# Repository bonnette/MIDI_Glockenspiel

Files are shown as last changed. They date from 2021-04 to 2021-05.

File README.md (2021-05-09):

# Arduino MIDI controlled Glockenspiel
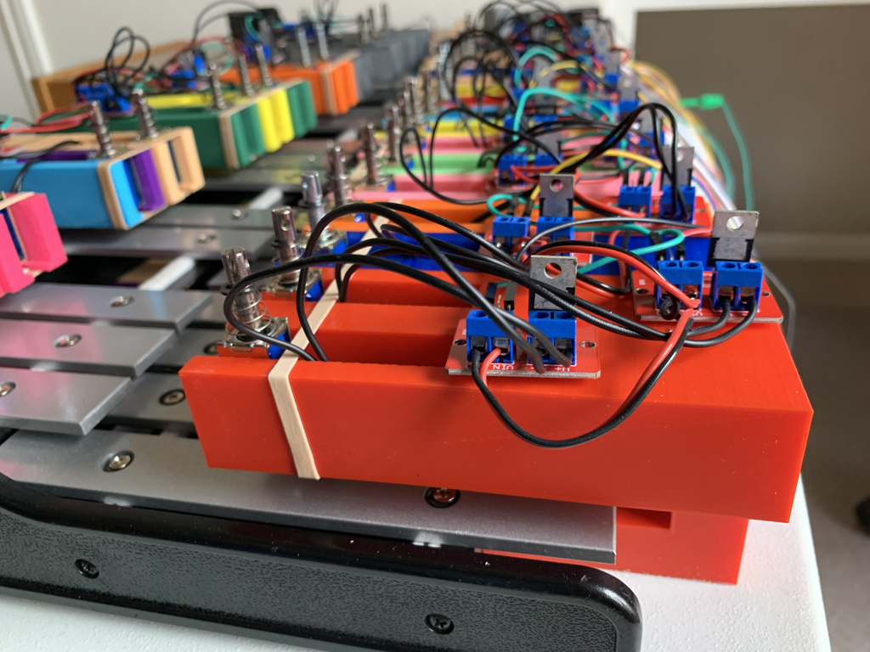
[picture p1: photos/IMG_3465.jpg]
Client Photo

<br/>
An automated Glockenspiel Arduino Project
Inspired by an Instructable
</br>
https://www.instructables.com/id/Making-the-Spielatron-Robotic-Glockenspiel/
</br>
See my AutoGlockenspiel repository for more information on my implementation of the "Instructable" project.</br>

The repository that you are currently looking at (although it was inspired by the Spielatron Instructable) is a totally different interpretation.
</br></br>
This project uses a Windows PC to drive an Arduino which fires one of 32 solenoids that sit above each note.
</br></br>
The MIDI control of the solenoids is accompished by using an Arduino Pro Mini. The serial connection between the Windows PC and the Arduino is through an FTDI interface. This interface allows music that has been converted to MIDI to be played on the Glockenspiel.
</br></br>
The Glockenspiel is a Pearl 32 note that I purchased from Ebay for $45
</br></br>
There is only one Arduino software program. This program uses the Arduino midi library to decode each MIDI note received from the PC. Then using I2C it sets one of 32 pins distributed across two MCP23017 I/O expander boards to a "HIGH" which then fires a solenoid that then strikes a note on the glockenspiel.</br>
The current program allows only one note at a time to be played. The use of LMMS on the PC provides you with the opportunity to direct MIDI to the Arduino on one track while the other tracks play on the computer. This makes for a very pleasant experience in that, you can listen to the glockenspiel along with the accompanying instruments playing on the PC. 
</br></br>
I designed holders for the solenoids. These holders fit on the bottom rails of the glockenspiel and align the solenoids over the keys. There are five different holders. Each holder takes approximately 4 hours to print. The difference in the holders is their location on the glockenspiel. There are three corner holders that hold two solenoids each. There are "High" holders which are all the same and there are "Low" holders. These are all the same as well. </br></br>
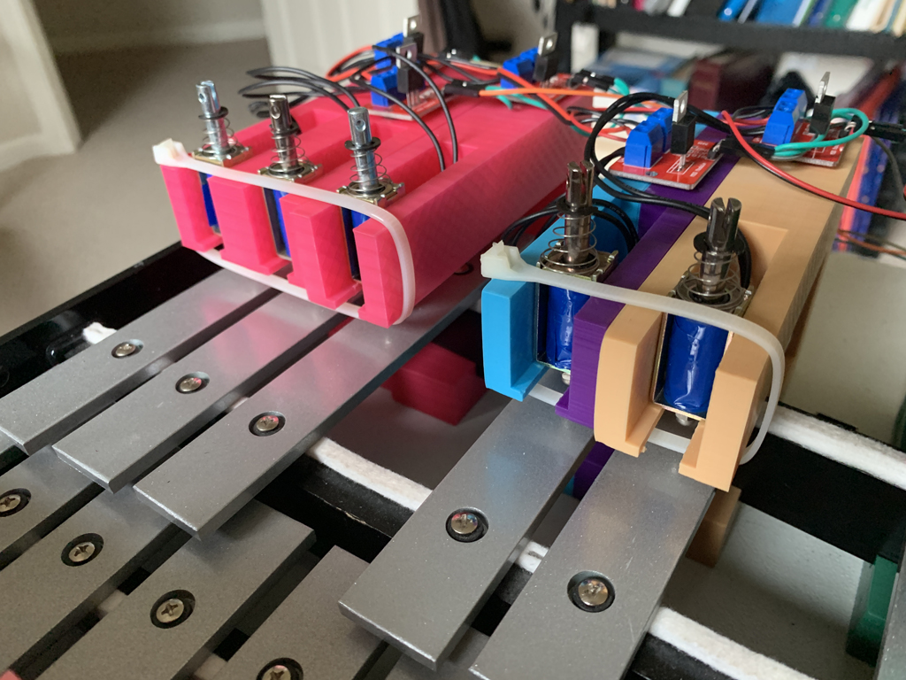
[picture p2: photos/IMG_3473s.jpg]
Client Photo

<br/>
The solenoids are held in place using zip ties.(Shown above). The zip ties are tied tight enough to hold the solinoids snuggly. 
</br></br>
A video of the glockenspiel playing a tune can be found here:</br>
https://youtu.be/QgNRVtduxMg
</br></br>
I used Fusion360 for the design of the solenoid holders and I thank Autodesk for allowing makers such as myself to use Fusion360 free of charge. Thanks Autodesk !</br>
I would also like to thank the developers of LMMS (https://lmms.io/) for their work.</br>
Thanks to hairless-midi (https://projectgus.github.io/hairless-midiserial/) for developing the Hairless MIDI Serial Bridge.</br>
and I also thank Tobias Erichsen for developing loopMIDI (https://www.tobias-erichsen.de/software/loopmidi.html). His software creates virtual loopback MIDI-ports which can then be used to connect the PC through a serial port (using the hairless-midi bridge) to the midi enabled glockenspiel.

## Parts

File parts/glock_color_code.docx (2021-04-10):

Note | Midi | Color | MCP Pin
F3 | 53 | Black | MCP A0 0
F3# | 54 | Brown | MCP A1 1
G3 | 55 | Red | MCP A2 2
G3# | 56 | Orange | MCP A3 3
A3 | 57 | Yellow | MCP A4 4
A3# | 58 | Green | MCP A5 5
B3 | 59 | Blue | MCP A6 6
C4 | 60 | Violet | MCP A7 7
C4# | 61 | Grey | MCP B0 8
D4 | 62 | White | MCP B1 9
D4# | 63 | Black | MCP B2 10
E4 | 64 | Brown | MCP B3 11
F4 | 65 | Red | MCP B4 12
F4# | 66 | Orange | MCP B5 13
G4 | 67 | Yellow | MCP B6 14
G4# | 68 | Green | MCP B7 15
A4 | 69 | Blue | MCP1 A0 0
A4# | 70 | Violet | MCP1 A1 1
B4 | 71 | Grey | MCP1 A2 2
C5 | 72 | White | MCP1 A3 3
C5# | 73 | Black | MCP1 A4 4
D5 | 74 | Brown | MCP1 A5 5
D5# | 75 | Red | MCP1 A6 6
E5 | 76 | Orange | MCP1 A7 7
F5 | 77 | Yellow | MCP1 B0 8
F5# | 78 | Green | MCP1 B1 9
G5 | 79 | Blue | MCP1 B2 10
G5# | 80 | Violet | MCP1 B3 11
A5 | 81 | Grey | MCP1 B4 12
A5# | 82 | White | MCP1 B5 13
B5 | 83 | Black | MCP1 B6 14
C6 | 84 | Brown | MCP1 B7 15

# MCP color code and pin assignment

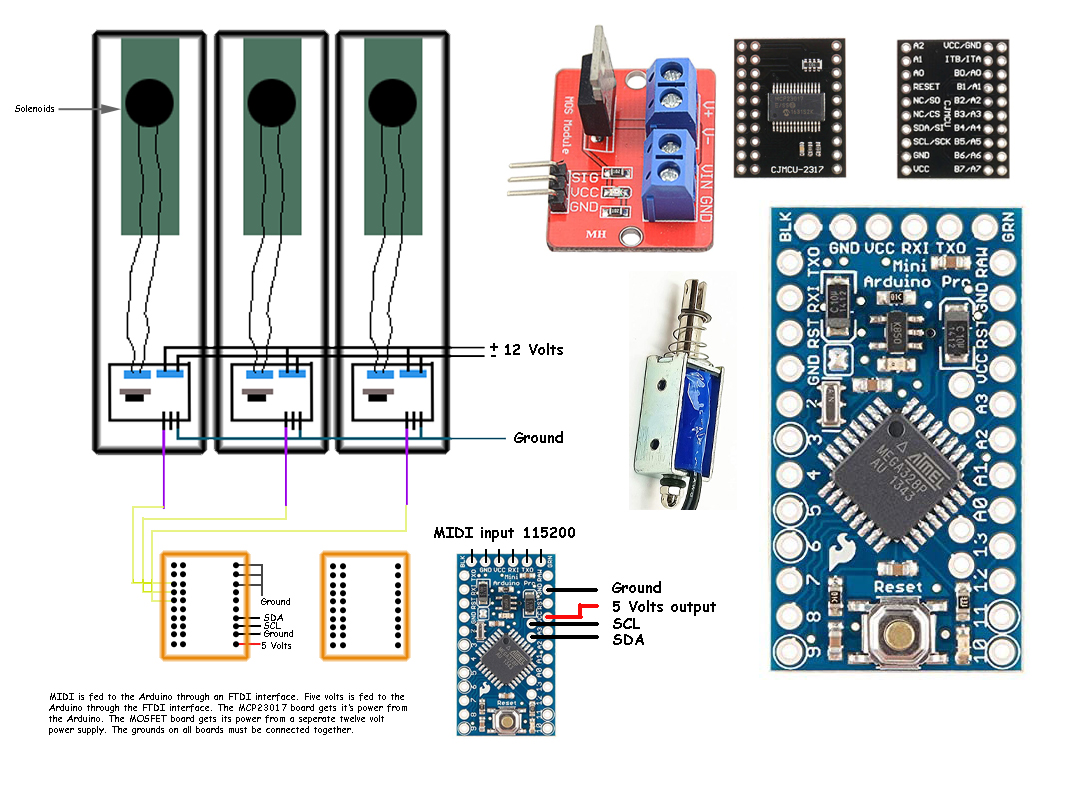
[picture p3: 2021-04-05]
parts/robo_glock.jpg

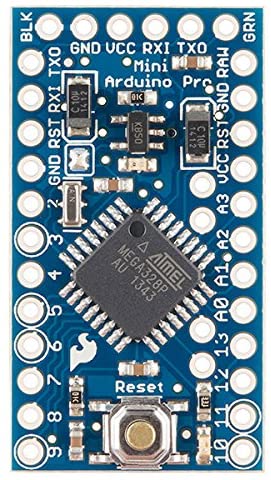
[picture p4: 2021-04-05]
parts/pro_mini.jpg

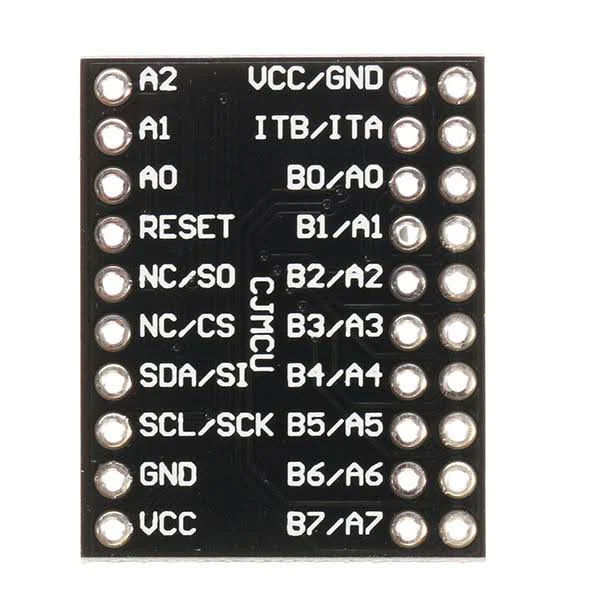
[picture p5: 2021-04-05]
parts/2317_back.jpg

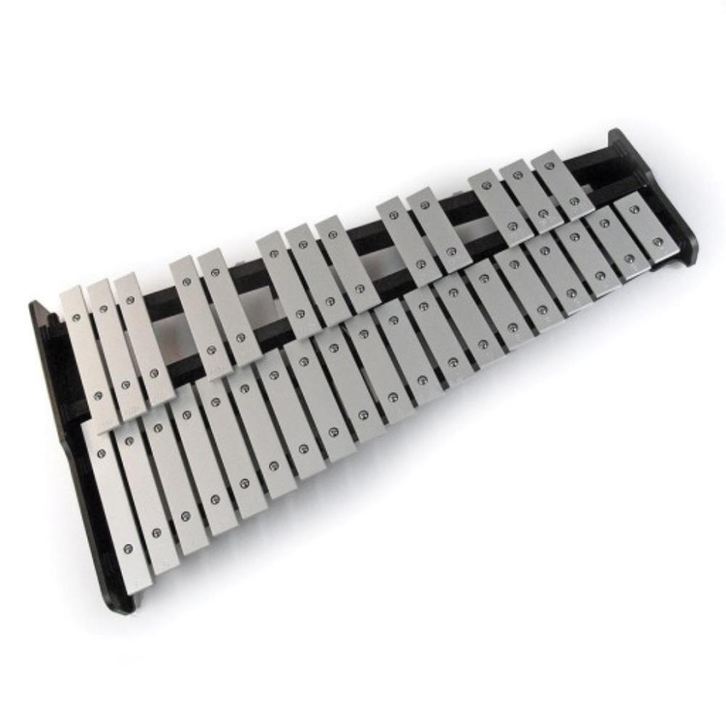
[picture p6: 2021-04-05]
parts/pearl_32.jpg

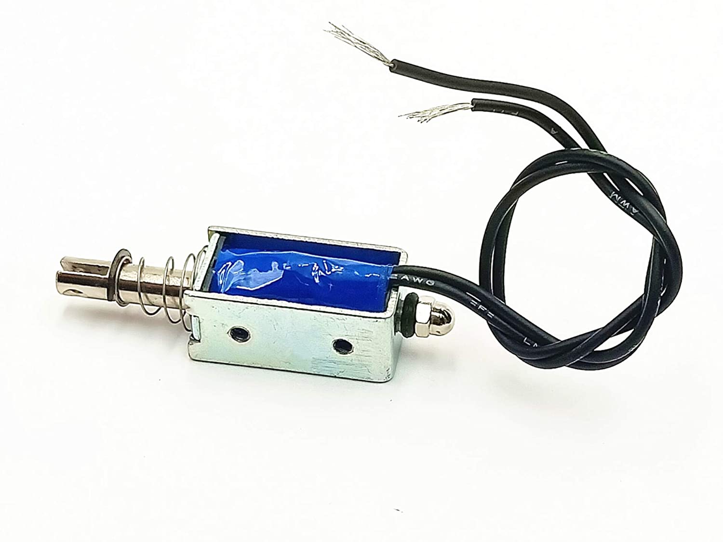
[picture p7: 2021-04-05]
parts/LYM_0530.jpg

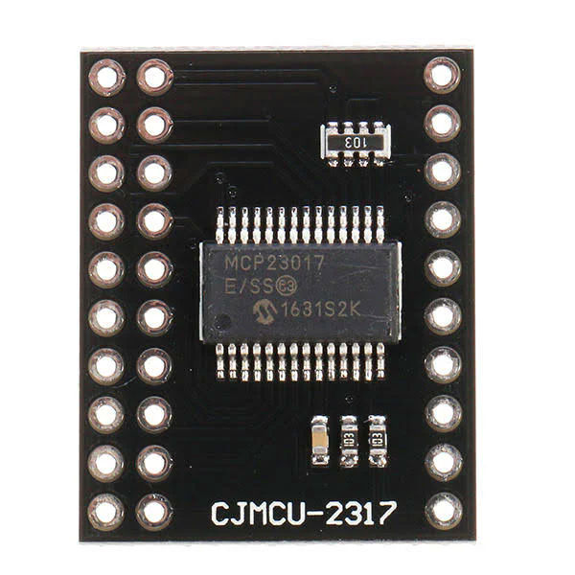
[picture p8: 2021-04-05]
parts/2317_front.jpg

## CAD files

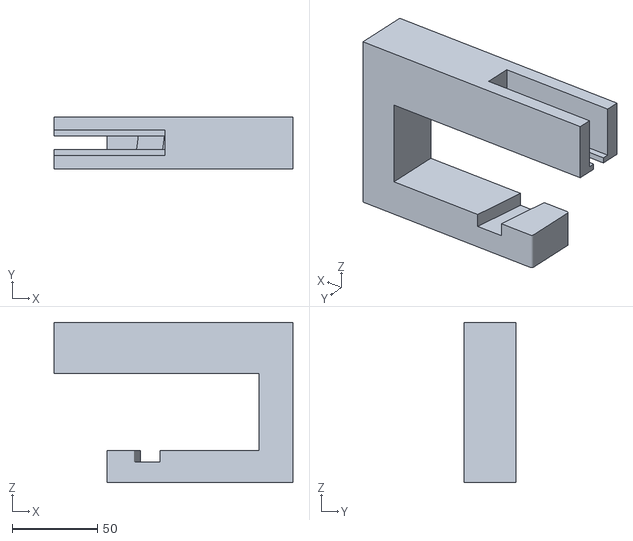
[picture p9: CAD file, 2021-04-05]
3D_printed/high_solenoid_hldr.stl
140.0 x 30.3 x 94.0

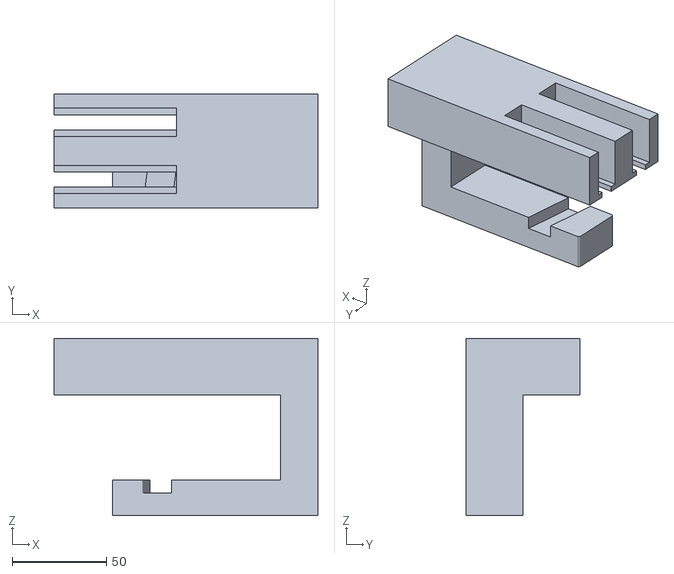
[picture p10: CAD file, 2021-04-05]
3D_printed/sol_hldr_hi_lft.stl
140.0 x 60.6 x 94.0

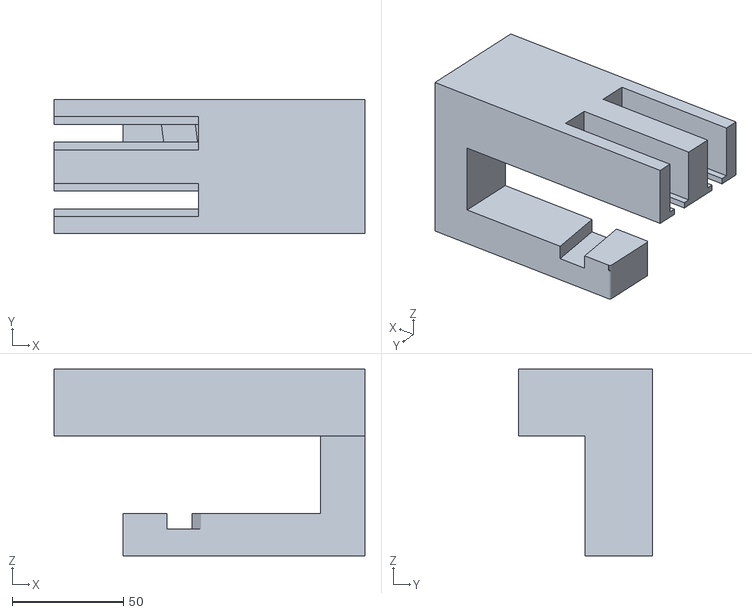
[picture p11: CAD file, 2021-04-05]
3D_printed/sol_hldr_lo_lft.stl
140.0 x 60.3 x 84.0

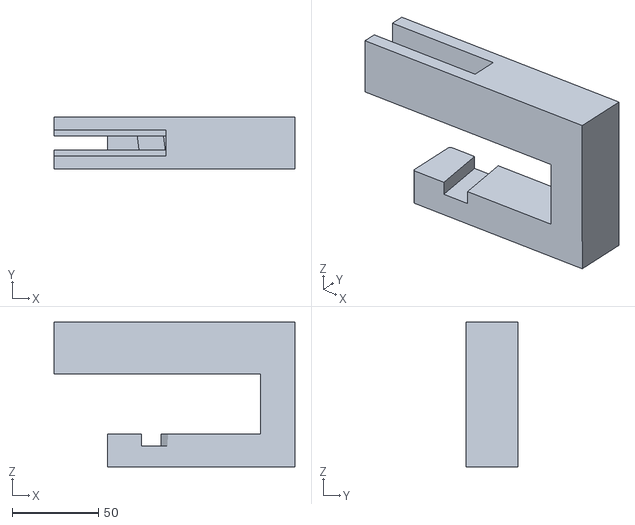
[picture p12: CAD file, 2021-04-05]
3D_printed/solenoid_hldr.stl
140.0 x 30.3 x 84.0

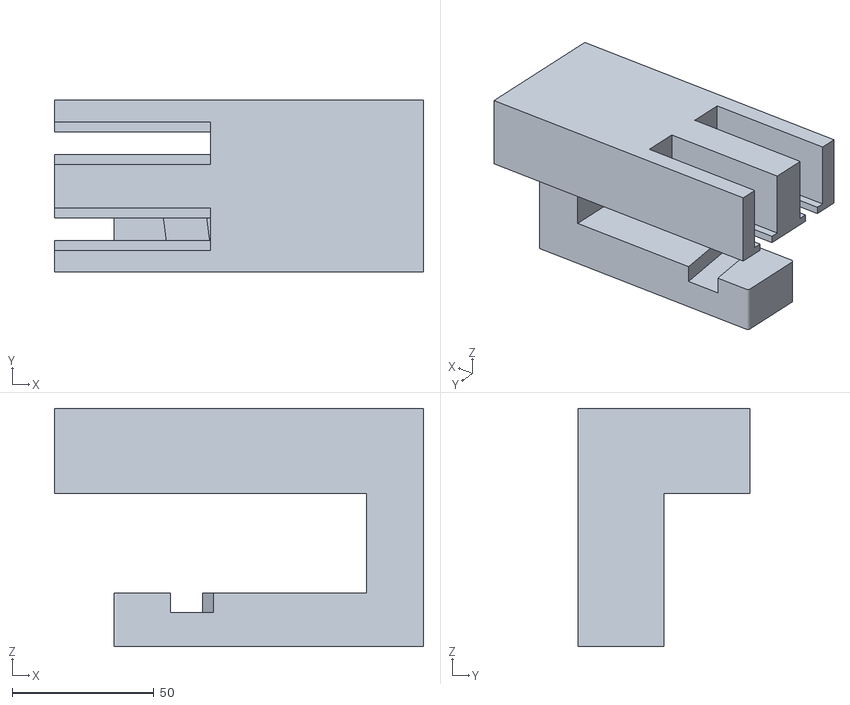
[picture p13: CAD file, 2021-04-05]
3D_printed/sol_hldr_lo_rght.stl
130.0 x 60.6 x 84.0

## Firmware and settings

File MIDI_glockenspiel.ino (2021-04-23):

/*
 * Larry Bonnette 04/23/2021
 * fire a solenoid when a certain MIDI note is recieved
 * The solenoid is used to strike a note on a glockenspiel
 */

#include <Wire.h>
#include "Adafruit_MCP23017.h" //MCP23017 - i2c 16 input/output port expander
#include <MIDI.h>  // Add Midi Library

#define LED 13    // Arduino Board LED is on Pin 13

void ProgRel(); //Declare so it compiles


//Create an instance of the library with default name, serial port and settings
MIDI_CREATE_DEFAULT_INSTANCE();

int period = 13; // Part of non-blocking delay to turn off solenoid
unsigned long time_now = 0; // Part of non-blocking delay

// Create mcp object for first MCP23017 board
Adafruit_MCP23017 mcp;

// Create mcp1 object for second MCP23017 board
Adafruit_MCP23017 mcp1;
int pinRelease = 99;
int pinRelease1 = 99;
void setup() {
  pinMode (LED, OUTPUT); // Set Arduino board LED pin 13 to output
  
  MIDI.begin(MIDI_CHANNEL_OMNI); // Initialize the Midi Library.
  // OMNI sets it to listen to all channels.. MIDI.begin(2) would set it 
  // to respond to notes on channel 2 only.
  
  mcp.begin();      // Initialize the MCP23017 library to use default address 0 
  mcp1.begin(1);      // Initialize the second MCP23017 library to use address 21
  
  Serial.begin(115200); // Initialize the serial port to 115200 baud rate. This will be used for MIDI communication
  
  // setting multiple pins as OUTPUT
int outMin = 0; // Lowest output pin
int outMax = 15; // Highest output pin
for(int i=outMin; i<=outMax; i++)
{  
  mcp.pinMode(i, OUTPUT);
  mcp1.pinMode(i,OUTPUT);
}

  MIDI.setHandleNoteOn(MyHandleNoteOn); // This is important!! This command
  // tells the Midi Library which function you want to call when a NOTE ON command
  // is received. In this case it's "MyHandleNoteOn".
  
  MIDI.setHandleNoteOff(MyHandleNoteOff); // This command tells the Midi Library 
  // to call "MyHandleNoteOff" when a NOTE OFF command is received.
}

void loop() { // Main loop
  if (millis() >= time_now + period) // Part of non-blocking delay
  {
    time_now = 0;
    ProgRel(); //turns off the solenoid after the non-blocking delay
    }
  
  MIDI.read(); // Continuously check if Midi data has been received.
}

// MyHandleNoteON is the function that will be called by the Midi Library
// when a MIDI NOTE ON message is received.
// It will be passed bytes for Channel, Pitch, and Velocity
void MyHandleNoteOn(byte channel, byte pitch, byte velocity) {
  switch (pitch) {
    case 53:
    mcp.digitalWrite(0,HIGH);
    time_now = millis();
    pinRelease = 0;
    break;
    case 54:
    mcp.digitalWrite(1,HIGH);
    time_now = millis();
    pinRelease = 1;
    break;
    case 55:
    mcp.digitalWrite(2,HIGH);
    time_now = millis();
    pinRelease = 2;
    break;
    case 56:
    mcp.digitalWrite(3,HIGH);
    time_now = millis();
    pinRelease = 3;
    break;
    case 57:
    mcp.digitalWrite(4,HIGH);
    time_now = millis();
    pinRelease = 4;
    break;
    case 58:
    mcp.digitalWrite(5,HIGH);
    time_now = millis();
    pinRelease = 5;
    break;
    case 59:
    mcp.digitalWrite(6,HIGH);
    time_now = millis();
    pinRelease = 6;
    break;
    case 60:
    mcp.digitalWrite(7,HIGH);
    time_now = millis();
    pinRelease = 7;
    break;
  case 61:
    mcp.digitalWrite(8,HIGH);
    time_now = millis();
    pinRelease = 8;
    break;
   case 62:
    mcp.digitalWrite(9,HIGH);
    time_now = millis();
    pinRelease = 9;
    break;
   case 63:
    mcp.digitalWrite(10,HIGH);
    time_now = millis();
    pinRelease = 10;
    break;
    case 64:
    mcp.digitalWrite(11,HIGH);
    time_now = millis();
    pinRelease = 11;
    break;
    case 65:
    mcp.digitalWrite(12,HIGH);
    time_now = millis();
    pinRelease = 12;
    break;
    case 66:
    mcp.digitalWrite(13,HIGH);
    time_now = millis();
    pinRelease = 13;
    break;
    case 67:
    mcp.digitalWrite(14,HIGH);
    time_now = millis();
    pinRelease = 14;
    break;
    case 68:
    mcp.digitalWrite(15,HIGH);
    time_now = millis();
    pinRelease = 15;
    break;
    case 69:
    mcp1.digitalWrite(0,HIGH);  //Start accessing the second MCP23017
    time_now = millis();
    pinRelease1 = 0;
    break;
    case 70:
    mcp1.digitalWrite(1,HIGH);
    time_now = millis();
    pinRelease1 = 1;
    break;
    case 71:
    mcp1.digitalWrite(2,HIGH);
    time_now = millis();
    pinRelease1 = 2;
    break;
    case 72:
    mcp1.digitalWrite(3,HIGH);
    time_now = millis();
    pinRelease1 = 3;
    break;
    case 73:
    mcp1.digitalWrite(4,HIGH);
    time_now = millis();
    pinRelease1 = 4;
    break;
    case 74:
    mcp1.digitalWrite(5,HIGH);
    time_now = millis();
    pinRelease1 = 5;
    break;
    case 75:
    mcp1.digitalWrite(6,HIGH);
    time_now = millis();
    pinRelease1 = 6;
    break;
    case 76:
    mcp1.digitalWrite(7,HIGH);
    time_now = millis();
    pinRelease1 = 7;
    break;
    case 77:
    mcp1.digitalWrite(8,HIGH);
    time_now = millis();
    pinRelease1 = 8;
    break;
    case 78:
    mcp1.digitalWrite(9,HIGH);
    time_now = millis();
    pinRelease1 = 9;
    break;
    case 79:
    mcp1.digitalWrite(10,HIGH);
    time_now = millis();
    pinRelease1 = 10;
    break;
    case 80:
    mcp1.digitalWrite(11,HIGH);
    time_now = millis();
    pinRelease1 = 11;
    break;
    case 81:
    mcp1.digitalWrite(12,HIGH);
    time_now = millis();
    pinRelease1 = 12;
    break;
    case 82:
    mcp1.digitalWrite(13,HIGH);
    time_now = millis();
    pinRelease1 = 13;
    break;
    case 83:
    mcp1.digitalWrite(14,HIGH);
    time_now = millis();
    pinRelease1 = 14;
    break;
    case 84:
    mcp1.digitalWrite(15,HIGH);
    time_now = millis();
    pinRelease1 = 15;
    break;
  default:
    // if nothing else matches, do the default
    // default is optional
    break;
} 
  digitalWrite(LED,HIGH);  //Turn LED on
}

// MyHandleNoteOff is the function that will be called by the Midi Library
// when a MIDI NOTE Off message is received.
// It will be passed bytes for Channel, Pitch, and Velocity
// This routine is used to fulfill the note off sent to us. The "ProgRel" routine is the real solenoid release routine
void MyHandleNoteOff(byte channel, byte pitch, byte velocity) {
/*  if (pinRelease != 99){
  mcp.digitalWrite(pinRelease,LOW);
  pinRelease = 99; 
  }else
  if (pinRelease1 != 99) {
      mcp1.digitalWrite(pinRelease1,LOW);
  pinRelease1 = 99;
  }*/
  digitalWrite(LED,LOW);  //Turn LED off
}

void ProgRel() {
  if (pinRelease != 99){
  mcp.digitalWrite(pinRelease,LOW);
  pinRelease = 99; 
  }else
  if (pinRelease1 != 99) {
      mcp1.digitalWrite(pinRelease1,LOW);
  pinRelease1 = 99;
  }
  digitalWrite(LED,LOW);  //Turn LED off
}
